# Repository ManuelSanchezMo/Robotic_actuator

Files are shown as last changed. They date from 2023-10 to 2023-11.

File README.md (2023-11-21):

# Introduction

This repository contains the drawings, electronics schematics, firmware
and building instructions for a (almost) completely 3D printed robotic
actuator. The actuator is based in a 36 stator poles and 42
rotor/magnetic poles BLCD, whose output is attached to a 6:1 planetary
gearbox.

Views:

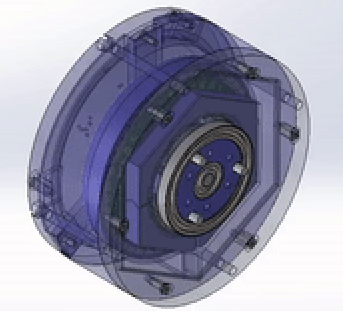
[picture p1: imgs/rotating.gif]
Fig 1. Perspective View
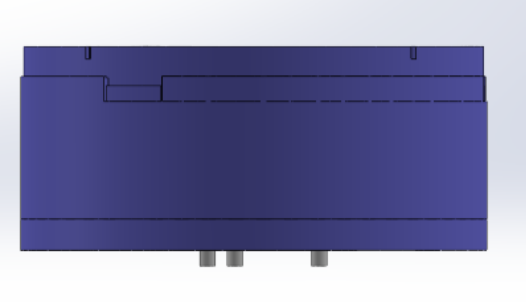
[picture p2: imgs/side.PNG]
Fig 2. Front View
|||
|---|---|
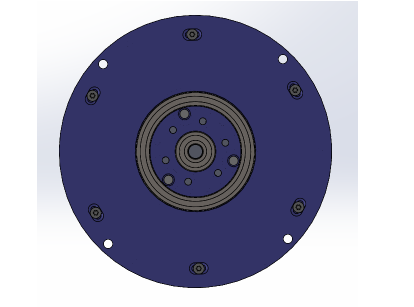
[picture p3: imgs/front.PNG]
Fig 3. Top View
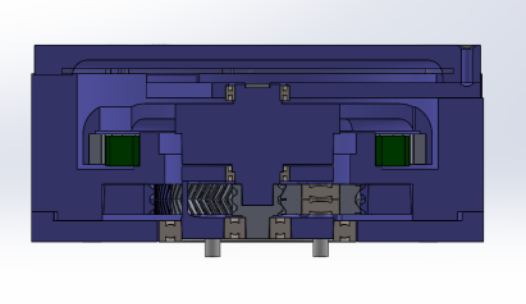
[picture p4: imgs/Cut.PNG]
Fig 4. Side View
| | |

# Bill of Materials

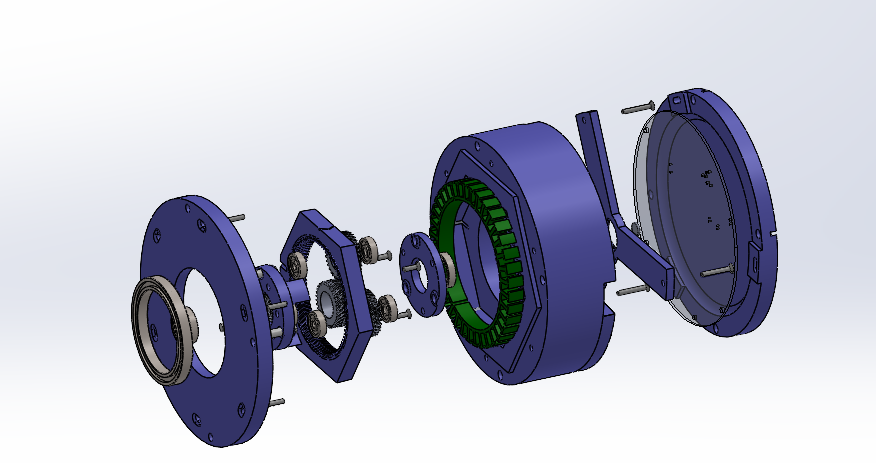
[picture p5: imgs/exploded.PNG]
side


  |Part Number   |  Part    |        Part Description    |    Quantity|
  ---------------|----------|---- -----------------------|------------|
  |1              | 30x5 mm steel pin   |Steel pins to improve torque transmsion|   3|
  |2               |61810-2RS|       50 x 65 x 7 mm ball bearing |     2|
  |3               |608-2RS|         8 x 22 x 7 mm ball  bearing|     2|
  |4               |61802-2RS |      15 x 24 x 5 mm ball bearing|    2|
  |5               |625-2RS1-SKF|    5 x 16 x 5 mm ball bearing|      6|
  |6               |Rotor Magnet|    10 x 4 x R51.5 mm  curved neodymium magnet|      42|
  |8              |M3 screw |       Torx flat head 10 mm screw|    3|
  |9               |M3 screw|        Torx flat head 14 mm screw|    6|
  |10              |M3 screw |       Torx flat head 20 mm screw|   3|
  |11              |10010 stator|    100mm x 78 mmx 10mm, 36 slots, steel stator|  1|

  : Bill of materials

# Controller

  ---------------------------------------------- --------------------------------------------
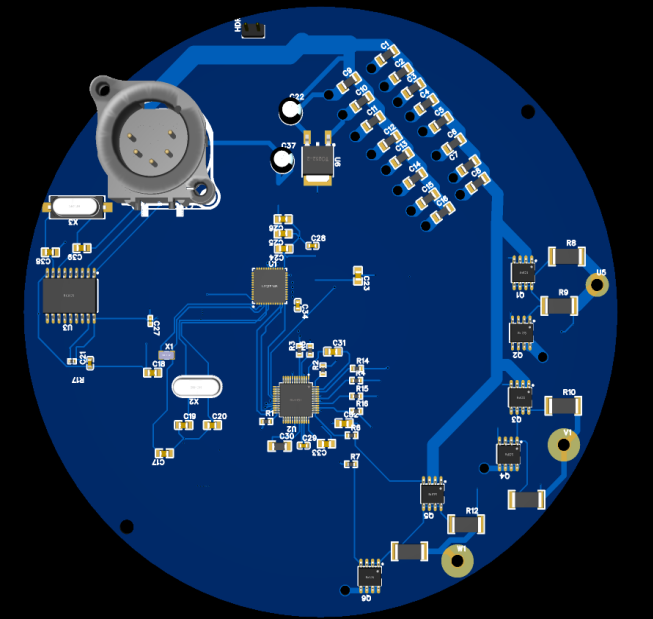
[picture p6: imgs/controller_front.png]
controller_front
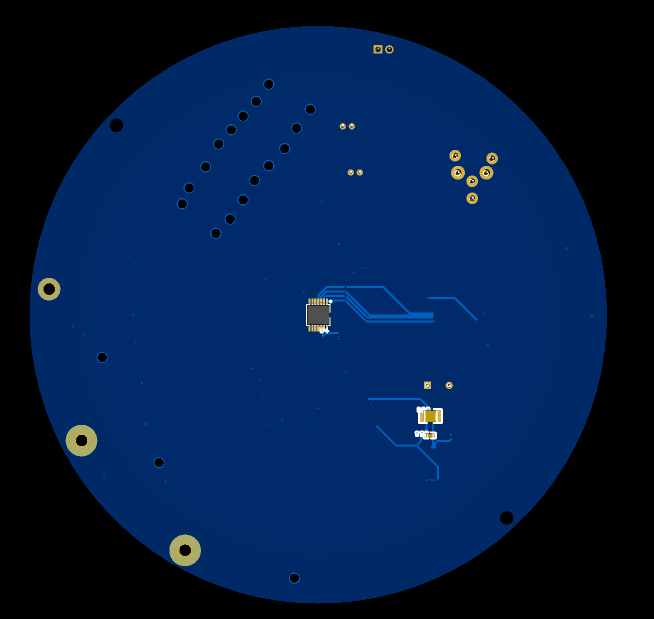
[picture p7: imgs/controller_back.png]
controller_back
    
  ---------------------------------------------- --------------------------------------------

|No.|Quantity|Comment |Designator |Footprint |Value|Manufacturer Part |Manufacturer |Supplier Part|Supplier|
|---|---|---|---|---|-----|---|---|---|---|
|1  |16 |10uF |C1,C2,C3,C4,C5,C6,C7,C8,C9,C10,C11,C12,C13,C14,C15,C16|C1206 | |CL31A106KBHNNNE |SAMSUNG |C13585 |LCSC |
|2  |5 |4.7uF |C17,C18,C19,C20,C23 |C0805 | |CS2012X7R475K350NRE |SamwhaCapacitor |C560882 |LCSC |
|3  |1 |10nF |C21 |C0603 | |CT41G-0603-2X1-50V-0.01uF-K(N)|TORCH |C136131 |LCSC |
|4  |2 |10uF |C22,C37 |CAP-TH_BD5.0-P2.00-D0.8-FD | |10uF50V5*7 |ValuePro |C45669 |LCSC |
|5  |3 |100nF |C24,C25,C26 |C0805 | |CL21F104ZBCNNNC |SAMSUNG |C1760 |LCSC |
|6  |1 |10nF |C27 |C0402 | |CL05B103KB5NNNC |SAMSUNG |C15195 |LCSC |
|7  |1 |1uF |C28 |C0603 | |CL10A105KB8NNNC |SAMSUNG |C15849 |LCSC |
|8  |1 |22nF |C29 |C0603 | |CL10B223KB8NNNC |SAMSUNG |C21122 |LCSC |
|9  |1 |100nF |C30 |C1206 | |CL31B104KCFNNNE |SAMSUNG |C1945 |LCSC |
|10 |3 |470nF |C31,C32,C33 |C0805 | |GRM21BR71C474KA01L |MurataElectronics |C408143 |LCSC |
|11 |1 |100nF |C34 |C0603 | |GRM188R71H104KA93D |MuRata |C77055 |LCSC |
|12 |1 |100nF |C35 |C0603 | |GRM188R71E104KA01D |MuRata |C77050 |LCSC |
|13 |1 |10uF |C36 |C1210 | |CL32B106KAJNNNE |SAMSUNG |C39232 |LCSC |
|14 |2 |22pF |C38,C39 |C0805 | |CL21C220JBANNNC |SAMSUNG |C1804 |LCSC |
|15 |1 |SIP2-2.54MM双排针|HDR1 |HDR-TH_2P-P2.54-V-M-R2-C1-S2.54 | |SIP2-2.54mm双排针 |null |C9900003705  |LCSC |
|16 |1 |NC5MAV |PS1 |CONN-TH_NC5MAV | |NC5MAV |NEUTRIK(优曲克) |C368510 |LCSC |
|17 |6 |IRF7470TRPBF  |Q1,Q2,Q3,Q4,Q5,Q6 |SO-8_L4.9-W3.9-P1.27-LS5.9-BL | |IRF7470TRPBF |InfineonTechnologies |C386356 |LCSC |
|18 |1 |0 |R1 |R0603 | |ERJ-3GEY0R00V |PANASONIC |C122704 |LCSC |
|19 |6 |2.2 |R2,R3,R4,R5,R6,R7 |R0603 | |RC0603FR-072R2L |YAGEO |C112307 |LCSC |
|20 |6 |0.03 |R8,R9,R10,R11,R12,R13 |R2512 | |MRF6432(2512)LR030FTS |SUP |C76247 |LCSC |
|21 |3 |10 |R14,R15,R16 |R0603 | |ERJ-3EKF10R0V |PANASONIC |C193335 |LCSC |
|22 |1 |10K |R17 |R0402 | |RMC10K103FTH |KAMAYA |C323692 |LCSC |
|23 |1 |STM32F411CEU6 |U1 |UFQFPN-48_L7.0-W7.0-P0.50-BL-EP | |STM32F411CEU6 |STMicroelectronics |C60420 |LCSC |
|24 |1 |TMC6200-TA |U2 |TQFP-48_L7.0-W7.0-P0.50-LS9.0-BL-EP| |TMC6200-TA |TRINAMICMotionControlGmbH|C915798 |LCSC |
|25 |1 |MCP2515T-I/SO |U3 |SOIC-18_L11.6-W7.5-P1.27-LS10.3-BL | |MCP2515T-I/SO |MICROCHIP |C153782 |LCSC |
|26 |1 |AS5048A-HTSP  |U4 |TSSOP-14_L5.0-W4.4-P0.65-LS6.4-BL  | |AS5048A-HTSP |美国AMS |C2153638 |LCSC |
|27 |3 |SEW_HOLE |U5,V1,W1 |SIMPLE_HOLE | | | | | |
|28 |1 |LD1086DT33TR  |U6 |TO-252-2_L6.5-W6.1-P4.58-LS10.0-TL | |LD1086DT33TR |STMicroelectronics |C12051 |LCSC |
|29 |1 |32.768KHz |X1 |FC-135R_L3.2-W1.5 | |Q13FC1350000400 |EPSON |C32346 |LCSC |
|30 |1 |25MHz |X2 |HC-49US_L11.5-W4.5-P4.88 | |XIHCELNANF-25MHZ |TAITIENElec |C295079 |LCSC |
|31 |1 |10MHz |X3 |HC-49-SMD_L12.0-W4.8 | |HC-49SM10MHz20pF30ppm |ZhejiangAbelElec |C150559 |LCSC |

# Firmware
The firmaware is developed with the Arduino IDE for the STM32 boards. It implements the Finite State Machine shown in the Fig 1, where (X) indicates state number and [X] the transition number. For the low level motion control the firmaware use the  Field Oriented Control (FOC) algorithm for Arduino [SimpleFOC](https://simplefoc.com/) The following dependencies  required:

* [SimpleFOC Arduino library](https://github.com/simplefoc/Arduino-FOC)
* [Library for CAN comunication](https://github.com/autowp/arduino-mcp2515/)
* [Finite State Machine library](https://github.com/kiwisincebirth/Arduino/blob/master/libraries/FSM/FiniteStateMachine.h)
*  [Custom can messages parser](/firmware/can_parser.zip)

<p align="center">
 <figure>
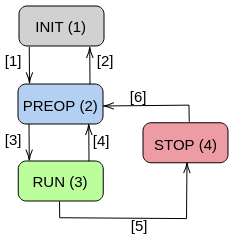
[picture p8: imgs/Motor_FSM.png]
  
  <figcaption>Fig 1. Finite Sate Machine of the actuator.</figcaption>
</figure> 
</p>

## CAN Protocol

|Frame |Signal|Bit Position|Bit Length|Scale|Offset|Units|Notes |
|---|---|---|---|-----|---|-----|---|
|0x001 | |<ul><li>0</li><li>16</li><li>32</li></ul>|<ul><li>16</li><li>16</li><li>16</li></ul>|<ul><li>0.125</li><li>0.125</li><li>0.125</li></ul>|<ul><li>0</li><li>0</li><li>0</li></ul>|<ul><li>-</li><li>-</li><li>-</li></ul>|<ul><li>P value for the PID position control</li><li>I value for the PID position control</li><li>D value for the PID position control</li></ul>|
|0x002 | |<ul><li>0</li><li>16</li><li>32</li><li>48</li></ul>|<ul><li>16</li><li>16</li><li>16</li><li>16</li></ul>|<ul><li>0.125</li><li>0.125</li><li>0.125</li><li>0.125</li></ul>|<ul><li>0</li><li>0</li><li>0</li><li>0</li><li></ul>|<ul><li>-</li><li>-</li><li>-</li><li>rad/s</li></ul>|<ul><li>P value for the PID speed control</li><li>I value for the PID speed control</li><li>D value for the PID speed control</li><li>Speed limit</li></ul>|
0x003 |      |<ul><li>0</li><li>16</li><li>32</li><li>48</li></ul>|<ul><li>16</li><li>16</li><li>16</li><li>16</li></ul>|<ul><li>0.125</li><li>0.125</li><li>1</li><li>0.125</li></ul>|<ul><li>0</li><li>0</li><li>0</li><li>-4095</li><li></ul>|<ul><li>V</li><li>V</li><li>-</li><li>rad</li></ul>|<ul><li>Voltage limit for motor input</li><li>Voltage limit for aling in calibration</li><li>Calibration (1 skip, o calibrate)</li><li>Electric angle offset </li></ul>|
0x004 |      |<ul><li>0</li><li>16</li><li>32</li><li>48</li></ul>|<ul><li>16</li><li>16</li><li>16</li><li>16</li></ul>|<ul><li>0.125</li><li>0.125</li><li>1</li><li>0.125</li></ul>|<ul><li>-4095</li><li>-4095</li><li>-4095</li><li>-4095</li><li></ul>|<ul><li>V</li><li>V</li><li>I</li><li>rad</li></ul>|<ul><li>Ua component of voltage input</li><li>Ub component of voltage input</li><li>Current drawn by motor</li><li>Electric angle  </li></ul>|
0x005 |      |<ul><li>0</li><li>16</li><li>32</li></ul>|<ul><li>16</li><li>16</li><li>16</li></ul>|<ul><li>0.125</li><li>0.125</li><li>0.125</li></ul>|<ul><li>-4095</li><li>-4095</li><li>-4095</li><li></ul>|<ul><li>rad</li><li>rad</li><li>rad/s</li></ul>|<ul><li>Current mechanical angle</li><li>Mechanical angle setponit</li><li>Shaft speed</li></ul>|
0x006 |      |<ul><li>0</li></ul>|<ul><li>16</li></ul>|<ul><li>1</li></ul>|<ul><li>0</li></ul>|<ul><li>-</li></ul>|<ul><li>Finite State Machine transition</li></ul>|
0x007 |      |<ul><li>0</li></ul>|<ul><li>16</li></ul>|<ul><li>0.125</li></ul>|<ul><li>-4095</li></ul>|<ul><li>rad</li></ul>|<ul><li>Motor set point command</li></ul>|

## DRIVERS
Custom [Python](https://github.com/ManuelSanchezMo/Robotic_actuator_python_driver) and [ROS](https://github.com/ManuelSanchezMo/Robot_actuator_ROS_driver)  drivers are available for the device. 
# Buildin Instructions

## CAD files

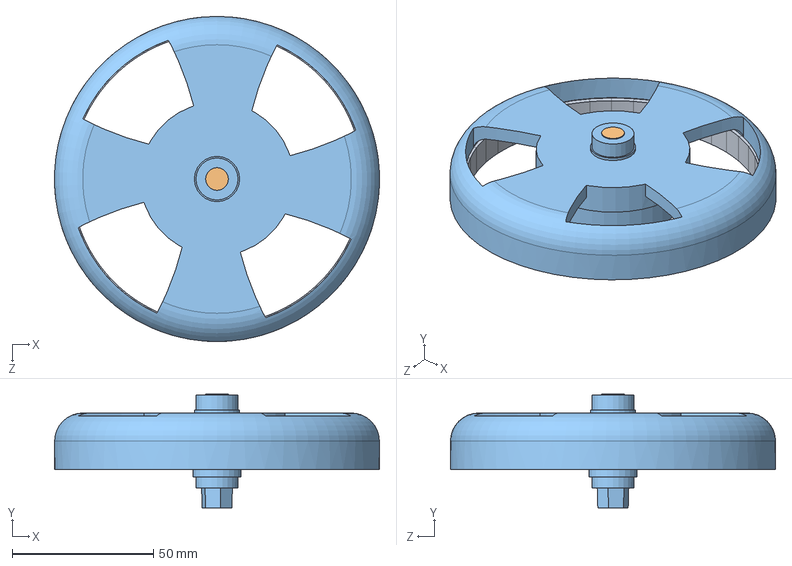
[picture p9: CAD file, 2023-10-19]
Rotor/Rotor_assembly.SLDASM
114.9 x 40.3 x 115.0 mm
rotor
encoder_mag
rotor_magnet x 42

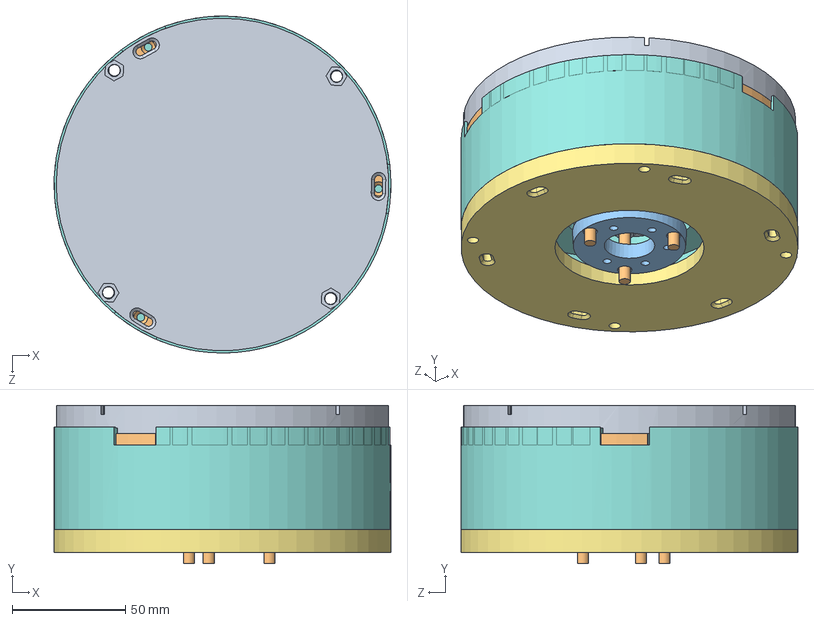
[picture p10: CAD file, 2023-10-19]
robot_actuator.SLDASM
149.0 x 70.0 x 149.0 mm
planet_carrier
30mm_pin x 3
planet_carrier_up
front_cover
estator
rotor
rotor_magnet x 42
encoder_mag
rotor_holder
back_cover

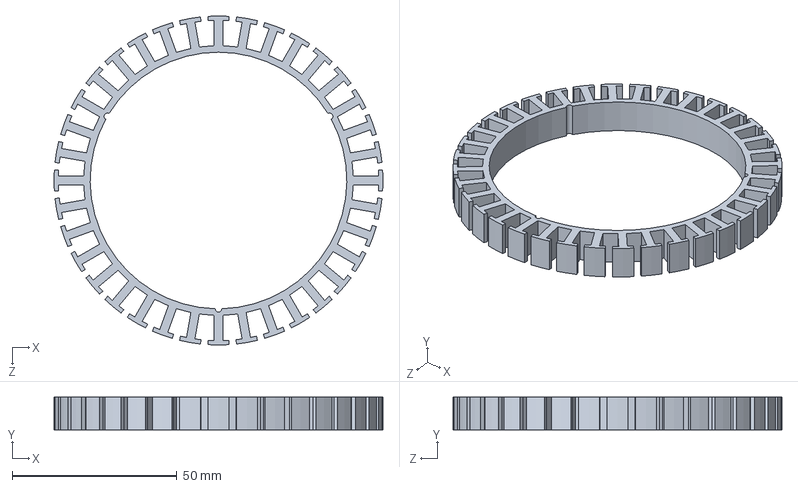
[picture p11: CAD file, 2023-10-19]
estator.SLDPRT
100.0 x 10.0 x 100.0 mm

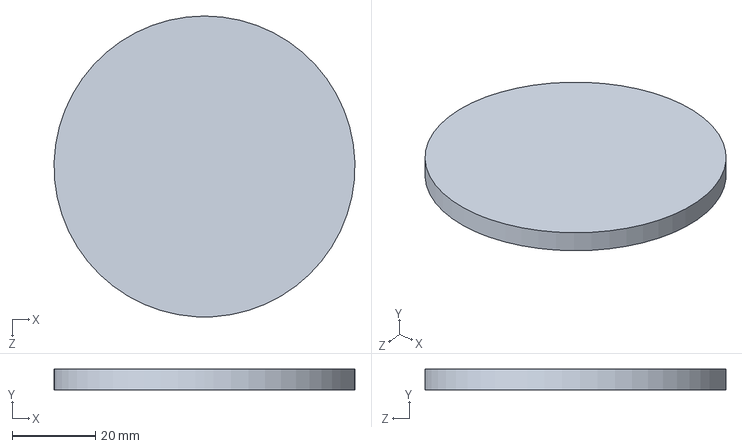
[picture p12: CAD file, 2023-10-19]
Planetary_gear/pieza_ring.SLDPRT
72.5 x 5.00 x 72.5 mm

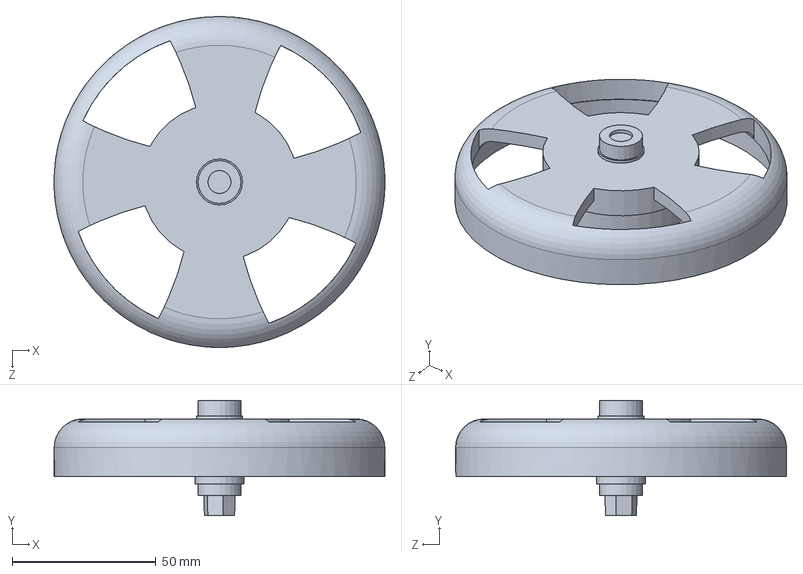
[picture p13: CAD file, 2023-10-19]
Rotor/rotor.SLDPRT
114.9 x 40.0 x 115.0 mm

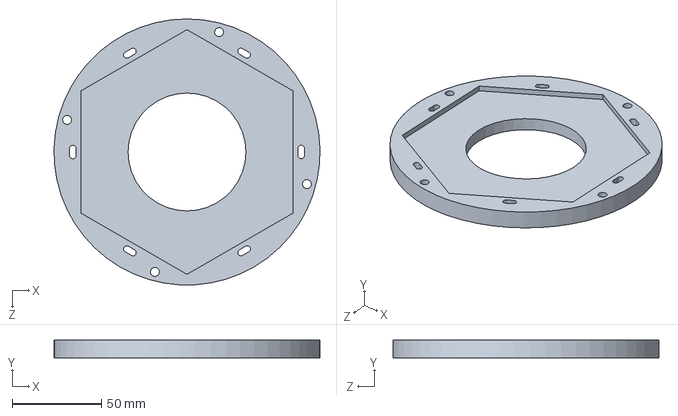
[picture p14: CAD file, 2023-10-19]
front_cover.SLDPRT
148.9 x 10.0 x 149.0 mm

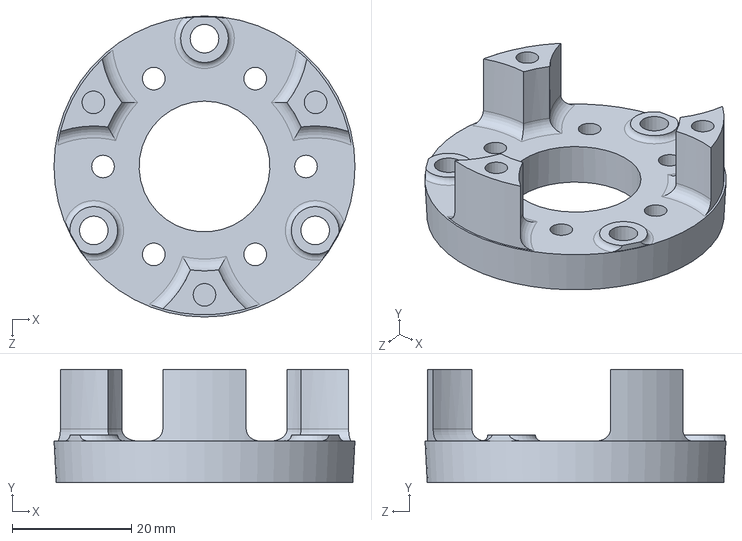
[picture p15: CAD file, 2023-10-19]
Planetary_gear/planet_carrier.SLDPRT
50.4 x 19.0 x 50.4 mm

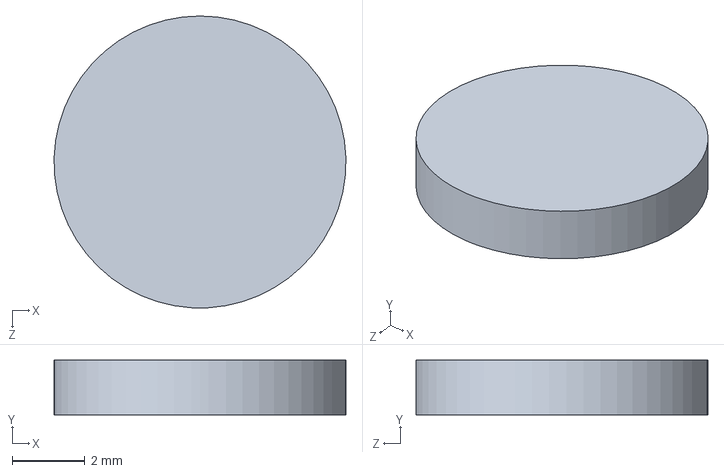
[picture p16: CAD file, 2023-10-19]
Rotor/encoder_mag.SLDPRT
8.00 x 1.50 x 8.00 mm

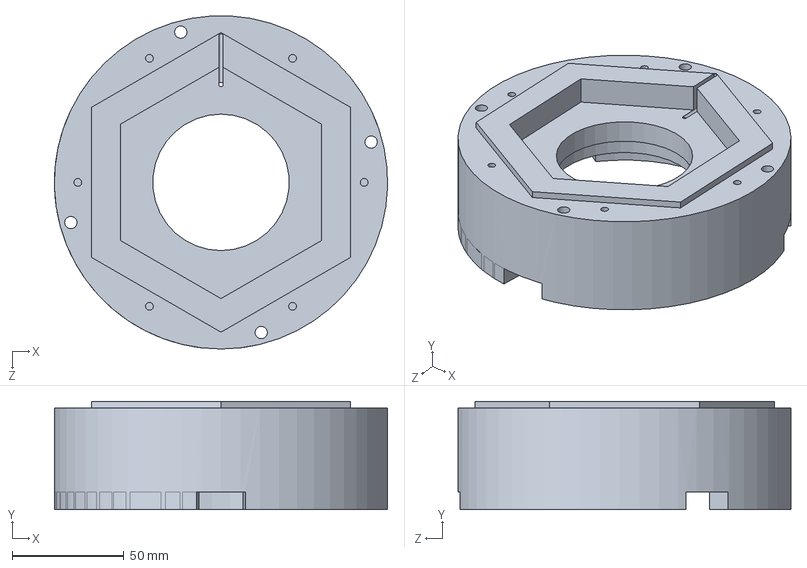
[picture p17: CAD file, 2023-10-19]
body.SLDPRT
148.9 x 48.5 x 148.9 mm

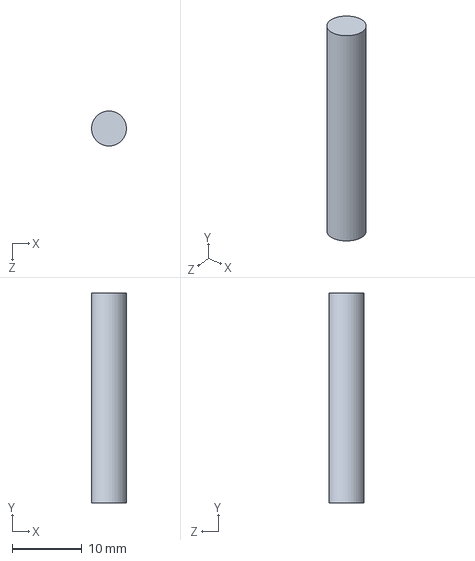
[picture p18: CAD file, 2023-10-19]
Planetary_gear/30mm_pin.SLDPRT
4.98 x 30.0 x 5.00 mm

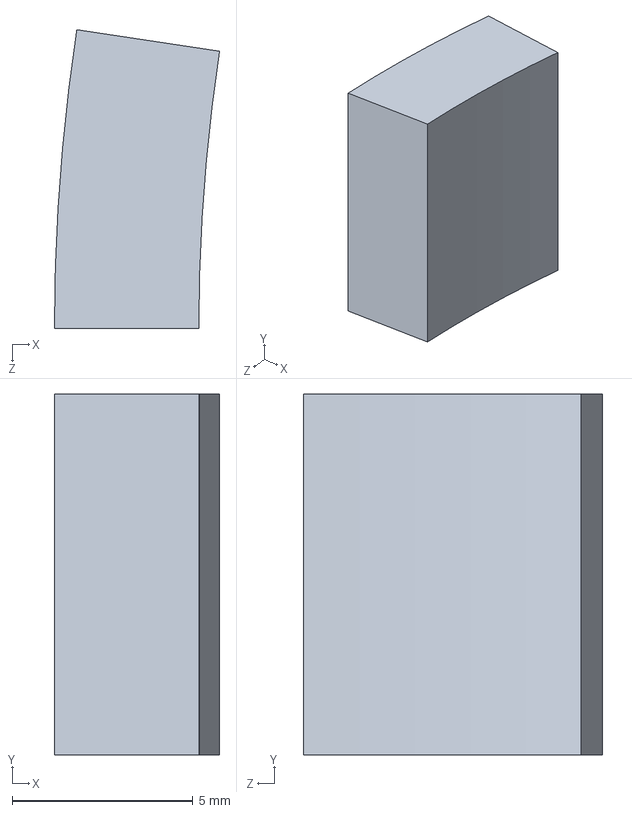
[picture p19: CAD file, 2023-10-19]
Rotor/rotor_magnet.SLDPRT
4.58 x 10.0 x 8.27 mm

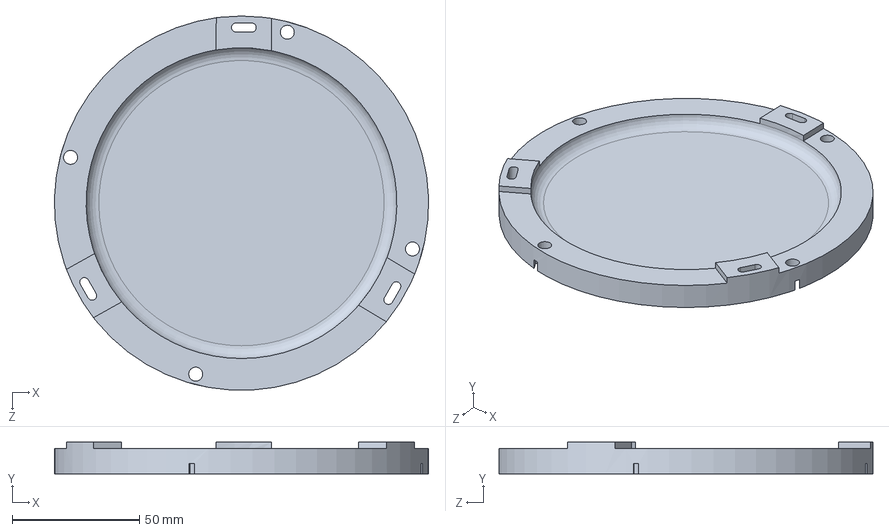
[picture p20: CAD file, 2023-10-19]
back_cover.SLDPRT
146.9 x 12.5 x 146.9 mm

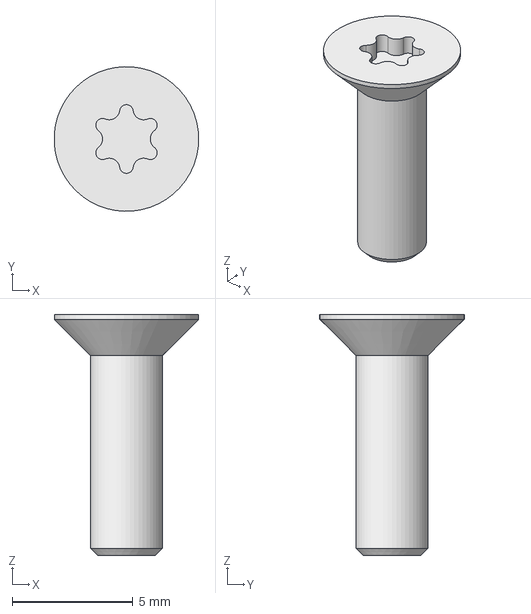
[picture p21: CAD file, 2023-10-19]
Planetary_gear/torx_flat_head_M3x10.step
5.99 x 6.00 x 10.0 mm

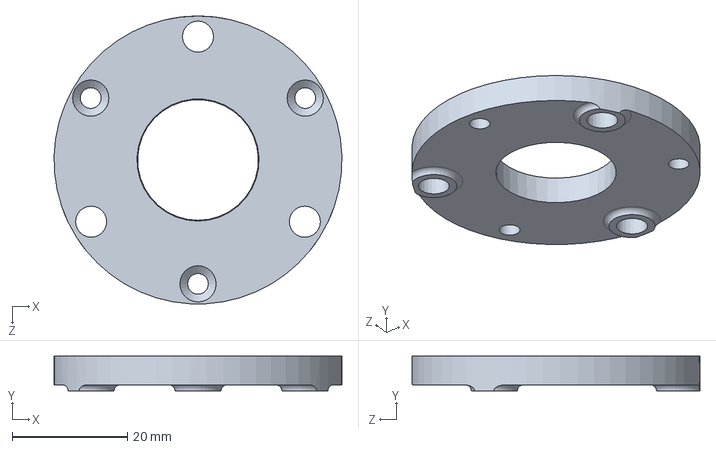
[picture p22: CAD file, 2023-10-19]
Planetary_gear/planet_carrier_up.SLDPRT
50.0 x 6.00 x 50.0 mm

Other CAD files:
rotor_holder.SLDPRT
pcb_controller.step
screws/torx_socket_countersunk_flat_head_M3x20.step
screws/torx_socket_countersunk_flat_head_M3x14.step

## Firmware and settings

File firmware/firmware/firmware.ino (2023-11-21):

#include <SPI.h>
#include <mcp2515.h>      //Library for using CAN Communication (https://github.com/autowp/arduino-mcp2515/)

#include <FiniteStateMachine.h>
#include <SimpleFOC.h>
#include <can_parser.h>

#define   INH_A PB_3
#define   INH_B PB_4
#define   INH_C PB_5
#define   EN_GATE PA_2
#define   M_PWM PB_7 
#define   M_OC PC_15
#define   OC_ADJ PC_14

struct can_frame canMsg;
//Can and sensor Cs SPI pin config
int Cs_pin_can= PA_7;
 MCP2515 mcp2515(Cs_pin_can);
int Cs_pin_encoder = PB_0;
MagneticSensorSPI sensor = MagneticSensorSPI(AS5048_SPI, Cs_pin_encoder);
//motor instance
int nPolePairs=21;
BLDCMotor motor = BLDCMotor(nPolePairs);
int8_t mec_out_dcl= 6, elec_out_dcl = 8; 
// driver instance
BLDCDriver3PWM driver = BLDCDriver3PWM(INH_A, INH_B, INH_C, EN_GATE);
//Default motorparam
float P_vel = 10.0, I_vel = 0.02, D_vel = 0.0, V_aling = 2.0, Vel_lim = 20.0, Volt_lim = 20.0;
float P_controller = 10.0, I_controller = 0.1, D_controller = 0.0, calibrate = 0.0, zero_angle_elec = 0.0;
float cmd_angle = 0;
//Finite state machine states
State INITIALIZATION = State(initMotorFSM); 
State PREOPERATIONAL = State(preopMotorFSM);
State OPERATIONAL = State(runMotorFSM);
State STOPPED = State(stopMotorFSM);
FSM MotorFSM = FSM(INITIALIZATION);
//can frames
int motor_cobid = 10;
int motor_config_1_frame = 1;
int motor_config_2_frame = 2;
int motor_config_3_frame = 3;
int motor_out_elec_frame = 4;
int motor_out_mec_frame = 5;
int transition_frame = 6;
int motor_sp = 7;

void setup() {
//start serial, CAN and FSM
  Serial.begin(9600);
  Serial.println("setup!");
  mcp2515.reset();
  mcp2515.setBitrate(CAN_500KBPS, MCP_8MHZ); //Sets CAN at speed 500KBPS and Clock 8MHz
  mcp2515.setNormalMode();
  MotorFSM.update();

}
void loop() {
 
  if (mcp2515.readMessage(&canMsg) == MCP2515::ERROR_OK){ 

    int motor_frame = int(canMsg.can_id) - motor_cobid;
    switch (motor_frame) //switch to run callback for the target function
    {
      case 1:
        config1_fnc(canMsg);
        break;
      case 2:
        config2_fnc(canMsg);
        break;
      case 3:
        config3_fnc(canMsg);
        break;
      case 6:
        Transition_FSM(int(canMsg.data[0]));
        break;
      case 7:
        set_sp_fnc(canMsg);
        break;
      default:
        break;
      }
  }
  if(MotorFSM.isInState(OPERATIONAL))  MotorFSM.update();  //run the motor callback (update foc) when the motor is in running mode
}

void config1_fnc(can_frame canConfigMsg){
  //Callback for config_1 
  Serial.println("Config 1 ");
  CONFIG_1_t* config_1;
  Unpack_CONFIG_1_can_parser(config_1, canMsg.data, canMsg.can_dlc );
  P_controller = config_1->P_control_phys;
  I_controller = config_1->I_control_phys;
  D_controller = config_1->D_control_phys;
  return;
}
void config2_fnc(can_frame canConfigMsg){
  //Callback for config_2
  Serial.println("Config 2 ");
  CONFIG_2_t* config_2;
  Unpack_CONFIG_2_can_parser(config_2, canMsg.data, canMsg.can_dlc );
  P_vel = config_2->P_vel_phys;
  I_vel = config_2->I_vel_phys;
  D_vel = config_2->D_vel_phys;
  Vel_lim = config_2->Vel_lim_phys;
  return;
}

void config3_fnc(can_frame canConfigMsg){
    //Callback for config_2
      Serial.println("Config 3 ");
      CONFIG_3_t* config_3;
      Unpack_CONFIG_3_can_parser(config_3, canMsg.data, canMsg.can_dlc );
      Volt_lim = config_3->Volt_lim_phys;
      V_aling = config_3->V_aling_phys;
      calibrate = config_3->Calibrate;
      zero_angle_elec = config_3->Zero_angle_elec_phys;
  return;
}
void set_sp_fnc(can_frame canConfigMsg){
  //Callback to set the set point 
  MOTOR_ANGLE_SP_t* angel_sp;
  Unpack_MOTOR_ANGLE_SP_can_parser(angel_sp, canMsg.data, canMsg.can_dlc );
  cmd_angle = angel_sp->angle_sp_phys;
  return;
}

void initMotorFSM(){
  //init motor. Always gets called on motor boot-up
  pinMode(PA_3, OUTPUT); //Pin CS - CAN
  pinMode(M_OC,OUTPUT);
  digitalWrite(M_OC,LOW);
  // M_PWM  - enable 3pwm mode
  pinMode(M_PWM,OUTPUT);
  digitalWrite(M_PWM,HIGH);
  sensor.init();
  // initialise magnetic sensor hardware
  // driver config
  motor.linkSensor(&sensor);
  pinMode(OC_ADJ,OUTPUT);
  digitalWrite(OC_ADJ,HIGH);
  // power supply voltage [V]
  driver.voltage_power_supply = 30;
  driver.init();
  // link the motor and the driver
  motor.linkDriver(&driver);
  // choose FOC modulation (optional)
  motor.foc_modulation = FOCModulationType::SpaceVectorPWM;
  // set motion control loop to be used
  motor.controller = MotionControlType::angle;
  Serial.println("in init!");
}

void preopMotorFSM(){
  //In preop motor, motor params are refreshed if where changed through config# message
  Serial.println("in preopMotorFSM!");
  // angle P controller
  motor.PID_velocity.P = P_vel;
  motor.PID_velocity.I = I_vel;
  motor.PID_velocity.D = D_vel;
  //maximal voltage to be set to the motor
  motor.voltage_limit = Volt_lim;
  motor.P_angle.P = P_controller; 
  motor.P_angle.I = I_controller;  // usually only P controller is enough 
  motor.P_angle.D = D_controller;  // usually only P controller is enough   
  motor.velocity_limit = Vel_lim; // maximal velocity of the position control
  motor.voltage_sensor_align = V_aling; // maximal Volts during alingment
  motor.monitor_variables = _MON_TARGET | _MON_VEL | _MON_ANGLE |_MON_VOLT_Q|_MON_VOLT_D|_MON_CURR_Q|_MON_CURR_D; //vars to monitor
  motor.useMonitoring(Serial);
  motor.init();
  
  if(calibrate == 1.0){ //if not calibrate, use params sent
    motor.electrical_angle =  zero_angle_elec;
    motor.sensor_direction = Direction::CCW;
    motor.initFOC();
    }
  else motor.initFOC();
  cmd_angle = motor.shaft_angle; //Current angle as command so the motor doesnt move on start
  motor.enable();
  Serial.println("Motor ready.");
}

void runMotorFSM(){
  //On Run loop  FOC and send out electric and mechanic params 
  motor.move(cmd_angle);
  motor.loopFOC();
  MOTOR_OUT_MEC_t* mec_out;
  can_frame canMsg_mec_out;
  mec_out->shaft_angle_phys = motor.shaft_angle; 
  mec_out->shaft_angle_sp_phys = motor.shaft_angle_sp; 
  mec_out->shaft_velocity_phys = motor.shaft_velocity; 
  __CoderDbcCanFrame_t__* cframe;
  Pack_MOTOR_OUT_MEC_can_parser(mec_out, cframe);
  canMsg_mec_out.can_id = motor_out_mec_frame + motor_cobid;
  canMsg_mec_out.can_dlc = mec_out_dcl;
  uint8_t i; for (i = 0; (i < mec_out_dcl) ;canMsg_mec_out.data[i] = cframe->Data[i]);
  mcp2515.sendMessage(MCP2515::TXB1, &canMsg_mec_out);

  MOTOR_OUT_ELEC_t* elec_out;
  can_frame canMsg_elec_out;
  elec_out->Ua_phys = motor.Ua;
  elec_out->Ub_phys = motor.Ub; 
  elec_out->current_phys = motor.current.q; 
  elec_out->electrical_angle_phys = motor.target; 
  __CoderDbcCanFrame_t__* cframe_mec;
  Pack_MOTOR_OUT_ELEC_can_parser(elec_out, cframe);
  canMsg_elec_out.can_id = motor_out_elec_frame + motor_cobid;
  canMsg_elec_out.can_dlc = elec_out_dcl;
  for (i = 0; (i < elec_out_dcl) ;canMsg_elec_out.data[i] = cframe_mec->Data[i]);
  mcp2515.sendMessage(MCP2515::TXB1, &canMsg_elec_out);
  Serial.println("in runMotorFSM!");
}

void stopMotorFSM(){
  Serial.println("in stopMotorFSM!");
  motor.disable();
}

void Transition_FSM(int transition)
{
    //Transition table for the FSM
    switch (transition)
    {
      case 1:
          if ( MotorFSM.isInState(INITIALIZATION)){
              MotorFSM.transitionTo(PREOPERATIONAL);
          }
          break;
      case 2:
          if ( MotorFSM.isInState(PREOPERATIONAL)){
              MotorFSM.transitionTo(INITIALIZATION);
          }
          break;
      case 3:
          if ( MotorFSM.isInState(PREOPERATIONAL) ){
            MotorFSM.transitionTo(OPERATIONAL);
          }
          break;
        case 4:
          if (  MotorFSM.isInState(OPERATIONAL) ){
            MotorFSM.transitionTo(PREOPERATIONAL);
          }
          break;
      case 5:
          if ( MotorFSM.isInState(OPERATIONAL)){
            MotorFSM.transitionTo(STOPPED);
          }  
          break;
      case 6:
          if ( MotorFSM.isInState(STOPPED)){
              MotorFSM.transitionTo(PREOPERATIONAL);
          } 
          break;
      default:
          break;
    }
    MotorFSM.update();
}

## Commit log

2023-10-19 Add controller data to readme
    [controller_bom.csv]
2023-10-20 Fix BOM controller table
2023-11-06 Add python driver code
2023-11-11 Add Finite state machine to python driver
